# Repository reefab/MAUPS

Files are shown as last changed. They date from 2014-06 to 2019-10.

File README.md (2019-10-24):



# MAUPS

MicroSlice Arduino Uno Pololu Shield.

As it says on the tin, this a shield to aggregate all the electronics for the [MicroSlice laser cutter](http://www.instructables.com/id/MicroSlice-A-tiny-Arduino-laser-cutter/).

I wasn't happy with the default electronic design of the project because I felt it was overly complicated by the creator's choice of using mostly off the shelf parts.

There isn't many components but a lot of connections and that made for a messy setup.

This [schematic](http://thelittlebox.co/theforum/viewtopic.php?f=8&t=13&sid=64e7ffe73cd25b9ab61adbdb73844c2a#p58) will demonstrate the issue clearly.

## What I wasn't happy with

 * Reliance on wires instead of using a PCB
 * Unnecessary voltage regulators (not sure why it initially used a 5V fan)
 * Unnecessary relays where a MOSFET would do
 * Separate Laser drive
 * Easydrivers instead of Pololus (mostly a personal preference but also a tad cheaper).

## What does MAUPS provides

### PCB

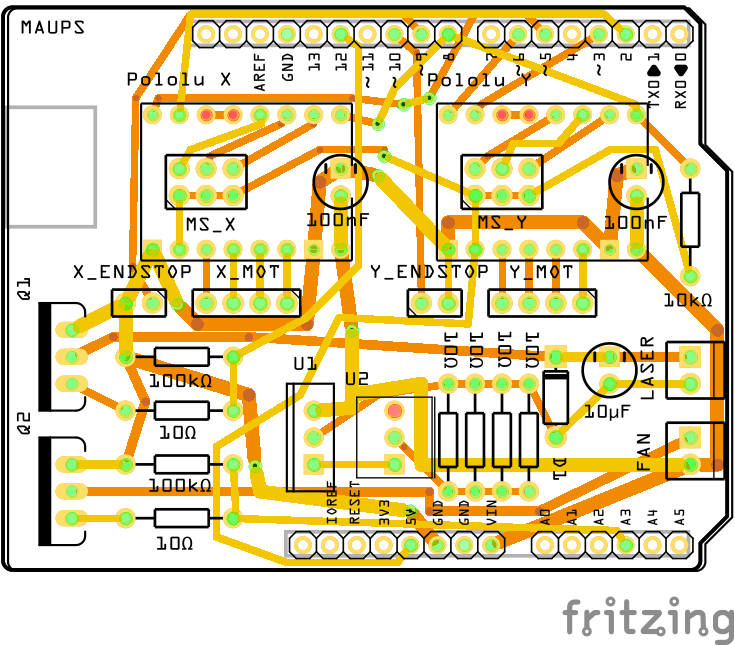
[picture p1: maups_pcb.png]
PCB


This is a shield for the Arduino Uno with everything plugging into it.

 * The 2 Pololus, replacing the 2 external easydrivers
 * The fan, without the external relay board or its voltage regulator board (if 5V)
 * The laser, without it's driver board
 * The motors
 * The endstops

Everything uses male Dupont connectors except for the laser and fan that uses screw terminals.

### Laser driver

The power supply for the laser is built-in into the shield. It's also controlled by a MOSFET now.
The power supply is based around a LM317 and requires a beefy radiator.

### Fan control

The fan is also controlled by a MOSFET.

## Bill of Materials

| Amount | Part Type | Properties | Notes |
|---|---|---|---|
| 2 | Electrolytic Capacitor | package 100 mil [THT, electrolytic]; capacitance 100nF; voltage 16V | |
| 1 | Electrolytic Capacitor | package 100 mil [THT, electrolytic]; capacitance 10µF; voltage 6.3V | |
| 1 | Rectifier Diode | package 300 mil [THT]; type Rectifier; part # 1N4001 | |
| 2 | Screw terminal - 2 pins | package THT; hole size 1.0mm,0.508mm; pins 2; pin spacing 0.1in (2.54mm) | |
| 4 | Generic single row female header - 8 pins | package THT; hole size 1.0mm,0.508mm; row double; form ♀ (female); pins 6; pin spacing 0.1in (2.54mm) | Pololus headers |
| 2 | Generic double row male header - 6 pins | package THT; hole size 1.0mm,0.508mm; row double; form ♂ (male); pins 6; pin spacing 0.1in (2.54mm) | Microstepping settings jumpers headers |
| 1 | Arduino Uno (Rev3) | type Arduino UNO (Rev3) | |
| 2 | Pololu A4988 | package SO16; chip label IC; variant variant 2 | |
| 2 | MOSFET-NCHANNEL | package to220v; variant pth2 | |
| 1 | 10k Ω Resistor | package THT; tolerance ±5%; bands 4; resistance 10kΩ; pin spacing 400 mil | |
| 6 | 10 Ω Resistor | package THT; tolerance ±5%; bands 4; resistance 10Ω; pin spacing 400 mil | |
| 1 | Trimmer Potentiometer | package THT; size Trimmer - 6mm; track Linear; type Trimmer Potentiometer; maximum resistance 100Ω | |
| 2 | 100k Ω Resistor | package THT; tolerance ±5%; bands 4; resistance 100kΩ; pin spacing 400 mil | |
| 1 | Voltage Regulator | package to220-adj; voltage 1.25 – 36 V; chip LM317; variant sink | |
| 2 | Male header - 2 pins | package THT; hole size 1.0mm,0.508mm; row single; form  ♂(male); pins 2; pin spacing 0.1in (2.54mm) | Stepper motors connectors|
| 2 | Male header - 4 pins | package THT; hole size 1.0mm,0.508mm; row single; form  ♂(male); pins 4; pin spacing 0.1in (2.54mm) | Endstop Connectors|

## To-do

 - [x] Prototype
 - [ ] Testing
 - [x] BOM
 - [ ] Assembly instruction
 - [ ] Publishing it on Fritzing and offering it up for sale

## Inspiration

 * [LOG](https://www.logre.eu/wiki/Micro_Découpeuse/Graveuse_Laser) Grenoble's hackerspace
 * [RAMPS](http://reprap.org/wiki/RAMPS_1.4) For the name and concept
 * And of course SilverJimmy for the design of the MicroSlice

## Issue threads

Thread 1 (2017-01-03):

Unclear BOM

Petraea, 2017-01-03:
Hi!
I'm working on rebuilding a laser engraver controller right now, and your design looks awesome for the job. However, I'm missing some details on your BOM, such as the type of MOSFET. Is this hidden in the Fritzing file? I'd love to see this in your README.

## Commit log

2014-06-25 * Fixed the fan's n-mosfet not being actually connected to ground .... ooops * Bigger traces for the hungrier connections, to be on the safe side * Labels with values instead of part numbers
    [maups.fzz]
2014-06-25 fixed pcb label
    [maups.fzz]
2014-06-25 Fixed some routing issues but need to edit the polulus parts to resolve the rest of the issues
    [maups.fzz]
2014-06-25 Redefined pololu part as through-hole, routing is much better now.
    [maups.fzz]
2014-06-25 deleted separate bom file
